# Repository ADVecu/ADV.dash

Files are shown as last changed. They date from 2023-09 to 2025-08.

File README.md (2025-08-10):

# ADV.dash

ADV.dash is a dashboard project built with **LVGL** and **ESP32-S3**.  
It is prepared to receive CAN bus data from **rusEFI** and, in the future, other programmable ECUs.

## Requirements
- PlatformIO
- ESP32-S3 DevKitC-1 board (1.5-inch display)
- LVGL library
- rusEFI CAN bus setup

## Compilation Steps
1. Clone the repository:
   ```bash
   git clone https://github.com/ADVecu/ADV.dash.git
   ```
2. Open the project in **PlatformIO**.
3. Copy the file `esp32-s3-devkitc-1-5inch` to the **boards** directory of the **Espressif** platform in PlatformIO.
4. Copy `lv_conf.h` to its correct LVGL configuration folder.
5. Build and upload the project to your ESP32-S3.

## Images
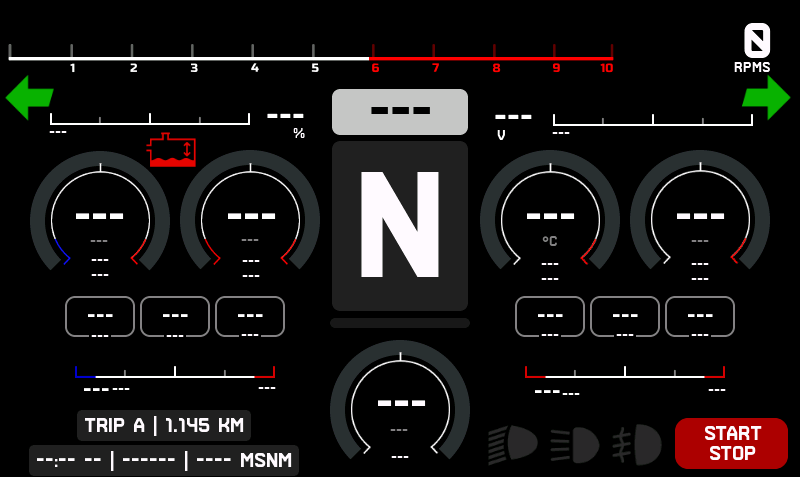
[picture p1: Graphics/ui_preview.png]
ADV.dash UI

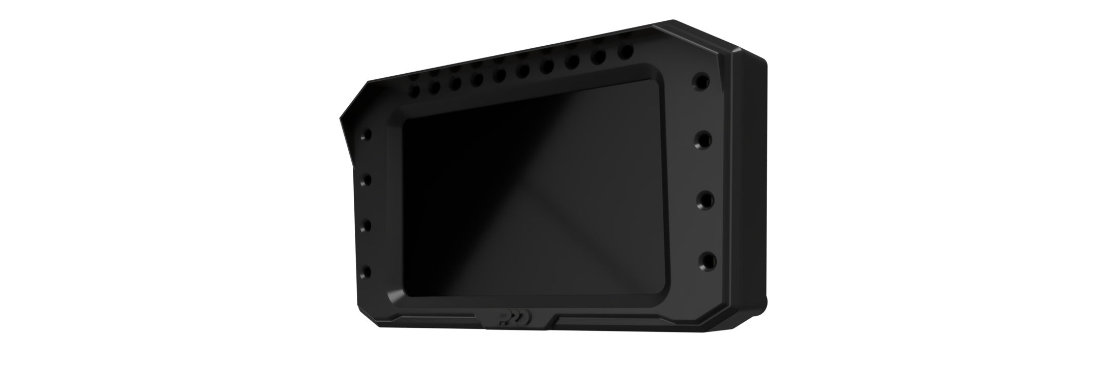
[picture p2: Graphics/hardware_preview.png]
ADV.dash Board


---

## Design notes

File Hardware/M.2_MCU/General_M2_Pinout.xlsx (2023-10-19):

 | MicroModule (M.2) Pinout v1.0 An Input is into the module. The module controls Outputs.
 |  | GND | 75 | Notes:
74 | 3.3V | G5 / BUS5 | 73 | All pins are 3.3V compatible unless otherwise specified. Don't expose any 3.3V pins to 5V.
72 | RTC_3V_BATT | G6 / BUS6 | 71 | Each MicroMod Processor Board has a GPIO controlled LED on the module not exposed to the board edge (aka LED_BUILTIN).
70 | G22 | G7 / BUS7 | 69 | A0/A1 should be assigned to pins that are exclusively ADC (no PWM capability)
68 | G21 | G8 | 67 | PWM0/PWM1 should be assigned to pins that are exclusively PWM (no ADC capability) D0/D1 should be assigned to pins that are exclusively GPIO (no ADC or PWM capability)
66 | G20 | G9 / ADC_D- / CAM_HSYNC | 65
64 | G19 | G10 / ADC_D+ / CAM_VSYNC | 63 | If the microcontroller lacks a specific pin function, and has left over GPIO, they can be over-ruled with
62 | G18 | SPI_CIPO (I) | 61 | GPIO. For example CTS/RTS can be overwritten with a GPIO if the microcontroller does not have flow control.
60 | G17 | SPI_COPI (O) | 59
58 | G16 | SPI_SCK (O) | 57
56 | G15 | SPI_CS# | 55
54 | G14 | I2C_SCL1 (I/O) | 53
52 | G13 | I2C_SDA1 (I/O) | 51
50 | G12 | BATT_VIN/3 (I - ADC) (0/3.3V) | 49
48 | G4 / BUS4 | PWM1 | 47
46 | G3 / BUS3 | GND | 45
44 | G2 / BUS2 | CAN_TX | 43
42 | G1 / BUS1 | CAN_RX | 41
40 | G0 / BUS0 | GND | 39
38 | A1 | USBHOST_D- | 37
36 | GND | USBHOST_D+ | 35
34 | A0 | GND | 33
32 | PWM0 | Module Key | 31
30 | Module Key | Module Key | 29
28 | Module Key | Module Key | 27
26 | Module Key | Module Key | 25
24 | Module Key | SWDIO | 23
22 | CAN2_TX | SWDCK | 21
20 | CAN2_RX | UART_RX1 (I) | 19
18 | D1 / CAM_TRIG | UART_TX1 (O) | 17
16 | I2C_INT# (I) | UART_CTS1 (I) | 15
14 | I2C_SCL (I/O) | UART_RTS1 (O) | 13
12 | I2C_SDA (I/O) | BOOT (I - Open Drain) | 11
10 | D0 | USB_VIN | 9
8 | G11 / SWDSWO | GND | 7
6 | RESET# (I - Open Drain) | USB_D- | 5
4 | 3.3V_EN | USB_D+ | 3
2 | 3.3V | GND | 1

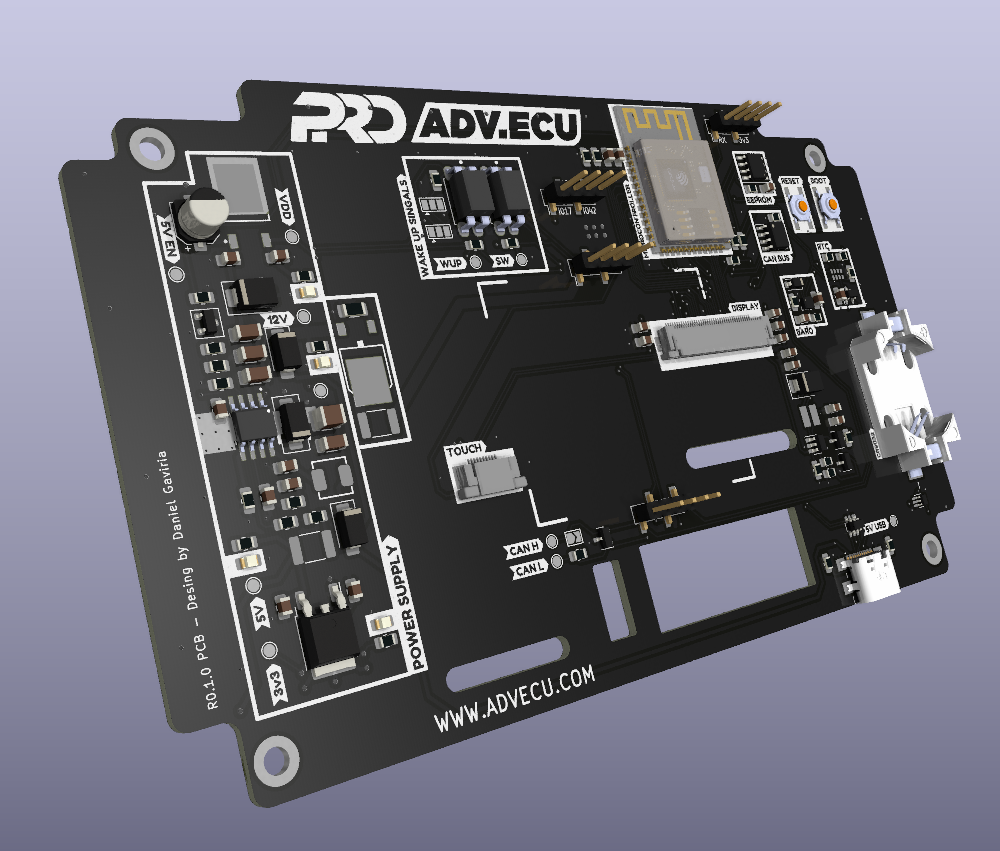
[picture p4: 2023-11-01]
Hardware/Dash/AdvDash_5_inch.png

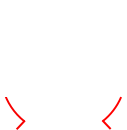
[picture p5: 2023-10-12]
SquerLine Project/assets/arcScaleRR.png

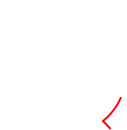
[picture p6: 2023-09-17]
SquerLine Project/assets/arcScale.png

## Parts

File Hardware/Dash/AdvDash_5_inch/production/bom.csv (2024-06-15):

Designator | Footprint | Quantity | Value | LCSC Part #
BT1 | BAT_CR2032-BS-6-1 | 1 | CR2032-BS-6-1 | C70377
C1, C12, C21, C23, C27, C7 | 0805 | 6 | 0.1uF | C38141
C10 | 1210 | 1 | 33uF | C531418
C11 | 1206 | 1 | 33uF | C342606
C13 | CP_Elec_5x5.4 | 1 | 100nF | C2992591
C14 | 0805 | 1 | 1uF - X7R | C116352
C15, C17 | 0805 | 2 | 22uF | C602037
C16, C20 | 0805 | 2 | 1uF | C28323
C18, C19 | 0805 | 2 | 100nF | C38141
C2, C22, C24, C25 | 0805 | 4 | 10uF | C15850
C26, C6 | 0805 | 2 | 10nF | C83170
C28, C29 | 0805 | 2 | 10uF | C1713
C3, C4 | 1206 | 2 | 4.7uF | C1872
C30, C31, C32, C33, C34, C35, C36, C37, C38, C39, C40, C41, C42, C43, C44, C45, C46, C47 | 0603 | 18 | 0.1uF | C577419
C5 | 1206 | 1 | 10nF | C106239
C8 | 0805 | 1 | 4.7nF | C1744
C9 | 0805 | 1 | 39pF | C1817
D1, D11 | D_SMA | 2 | 1N5819 | C437199
D10 | SOT-23 | 1 | BAS70-05 | C5189799
D12 | 0805 | 1 | LED | C965819
D13, D14, D15, D16, D17, D18, D19, D20, D21, D22, D23, D24, D25, D26, D27, D28, D29, D30 | LED_RGB_5050-6 | 18 | SK9822 | C2829089
D2 | D_SMA | 1 | B340 | C64982
D3, D4 | 0805 | 2 | LED | C965818
D5 | D_SMB | 1 | SMBJ20A | C151257
D6 | 0805 | 1 | LED | C965812
D7 | D_SMB | 1 | SS24BF | C35501
D8 | SOT-23 | 1 | NUP2105L | C5158054
D9 | D_SOD-123 | 1 | 1N4148W | C5345962
F1, F2 | 1812 | 2 | 3A 24V | C883154
G1 | INF-PG-TO252-3-11_N | 1 | TLF80511TF_V33
H1, H2, H3, H4 | MountingHole_3.2mm_M3_DIN965_Pad_TopBottom | 4 | MountingHole
H5, H6, H7 | MountingHole_2.5mm_Pad | 3 | MountingHole_Pad | C3020128
IC1 | RV8803C7 | 1 | RV-8803-C7 | C2846926
IC2, IC3 | SOT-353_SC-70-5_Handsoldering | 2 | 74HCT1G126GW,125 | C455064
J1 | 117348390 | 1 | 1-1734839-0 | C590935
J2 | 54104-4031 | 1 | 54104-4031 | C164172
J3 | USB4110GFA | 1 | USB4110-GF-A
J4, J6 | PinHeader_1x04_P2.54mm_Vertical_SMD_Pin1Left | 2 | 2.54mm 1x4
J5 | PinHeader_1x04_P2.54mm_Vertical_SMD_Pin1Left | 1 | UART0
JP1 | SolderJumper-2_P1.3mm_Open_TrianglePad1.0x1.5mm | 1 | 120ohm
JP2, JP3, JP4, JP6 | SolderJumper-3_P1.3mm_Open_Pad1.0x1.5mm | 4 | ACT +/-
JP5 | SolderJumper-3_P1.3mm_Open_Pad1.0x1.5mm | 1 | Reset Control
L1 | MDA4020-6R8M | 1 | 6.8uH | C2847472
L2 | TCK145 | 1 | 6.8uH | C167253
Q2 | SOT-23 | 1 | AO3401A | C15127
Q3 | SOT-23 | 1 | S8050 | C266592
R1, R12, R17, R2, R24, R26, R27, R35, R36, R7 | 0805 | 10 | 10K | C17414
R10 | 0805 | 1 | 0R | C17414
R13, R14 | 0805 | 2 | 1k3 | C2933303
R15 | 0805 | 1 | 10R | C25278
R16, R28, R29, R30, R31 | 0805 | 5 | 100k | C149504
R18 | 0805 | 1 | 100R | C17408
R19, R20 | 0805 | 2 | 4.7k | C17673
R21, R6 | 0805 | 2 | 0R | C17477
R22, R23 | 0805 | 2 | 5k1 | C84375
R25 | 0805 | 1 | 120 | C114245
R3 | 0805 | 1 | 332k | C212383
R32 | 0805 | 1 | 2k | C17604
R33, R34 | 0805 | 2 | 2K7 | C17530
R4 | 0805 | 1 | 68k1 | C5266070
R5 | 0805 | 1 | 49k9 | C17719
R8 | 0805 | 1 | 1k91 | C2999452
R9 | 1206 | 1 | 2K7 | C2907449
SW1, SW2 | SW_TL3342F160QG_TR | 2 | RESET | C2886898
T1 | D-PAK_TO252AA | 1 | IRFR5305 | C5155388
TP1 | TestPoint_Pad_D1.5mm | 1 | VIN_TP
TP10 | TestPoint_Pad_D1.5mm | 1 | CANH_TP
TP11 | TestPoint_Pad_D1.5mm | 1 | CANL_TP
TP2 | TestPoint_Pad_D1.5mm | 1 | EN_TP
TP3 | TestPoint_Pad_D1.5mm | 1 | EN_MCU_TP
TP4 | TestPoint_Pad_D1.5mm | 1 | USB_5VTP
TP5 | TestPoint_Pad_D1.5mm | 1 | 5V_TP
TP6 | TestPoint_Pad_D1.5mm | 1 | VDD_TP
TP7 | TestPoint_Pad_D1.5mm | 1 | 3.3V_TP
TP8 | TestPoint_Pad_D1.5mm | 1 | WAKE_UP_TP
TP9 | TestPoint_Pad_D1.5mm | 1 | SW12V_TP
U1 | ESP32-S3-WROOM-1 | 1 | ESP32-S3-WROOM-1-N4R8 | C2913200
U10, U9 | SOIC254P975X460-4N | 2 | PC817 | C3025164
U2 | CONV_TPS54331DDA | 1 | TPS54331DDA | C90761
U3 | SOT-23-6_Handsoldering | 1 | MT9201 | C182966
U4 | SOT-23-6 | 1 | USBLC6-2P6 | C7519
U5 | SOIC-8_3.9x4.9mm_P1.27mm | 1 | SN65HVD230 | C12084
U6 | Bosch_LGA-8_2x2.5mm_P0.65mm_ClockwisePinNumbering | 1 | BMP280 | C83291
U7 | SOIC-8-1EP_3.9x4.9mm_P1.27mm_EP2.29x3mm | 1 | CAT24C51 | C79986
U8 | TO-252-2 | 1 | LD1086DT33TR | C12051

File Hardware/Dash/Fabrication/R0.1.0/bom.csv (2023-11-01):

Designator | Footprint | Quantity | Value | LCSC Part #
BT1 | BAT_CR2032-BS-6-1 | 1 | CR2032-BS-6-1
C1, C12, C23, C27, C7 | 0805 | 5 | 0.1uF
C10 | 1210 | 1 | 33uF
C11 | 1206 | 1 | 33uF
C13 | CP_Elec_5x5.4 | 1 | 100nF
C14 | 0805 | 1 | 1uF - X7R
C15, C17 | 0805 | 2 | 22uF
C16, C20 | 0805 | 2 | 1uF
C18, C19 | 0805 | 2 | 100nF
C2, C22, C24, C25, C28, C29 | 0805 | 6 | 10uF
C21 | 0805 | 1 | 0.1uF | DNP
C26, C6 | 0805 | 2 | 10nF
C3, C4 | 1206 | 2 | 4.7uF
C30, C31, C32, C33, C34, C35, C36, C37, C38, C39, C40, C41, C42, C43, C44, C45, C46, C47 | 0603 | 18 | 0.1uF
C5 | 1206 | 1 | 10nF
C8 | 0805 | 1 | 4.7nF
C9 | 0805 | 1 | 39pF
D1, D11 | D_SMA | 2 | 1N5819
D10 | SOT-23 | 1 | BAS70-05
D12, D3, D4 | 0805 | 3 | LED
D13, D14, D15, D16, D17, D18, D19, D20, D21, D22, D23, D24, D25, D26, D27, D28, D29, D30 | LED_WS2812B_PLCC4_5.0x5.0mm_P3.2mm | 18 | WS2812B
D2 | D_SMA | 1 | B340
D5 | D_SMB | 1 | SMBJ20A
D6 | 0805 | 1 | LED | DNP
D7 | D_SMB | 1 | SS24BF
D8 | SOT-23 | 1 | NUP2105L
D9 | D_SOD-123 | 1 | 1N4148W
F1 | 1812 | 1 | 3A 24V
F2 | 1812 | 1 | 3A 24V | C883140
G1 | INF-PG-TO252-3-11_N | 1 | TLF80511TF_V33
H1, H2, H3, H4 | MountingHole_3.2mm_M3_DIN965_Pad_TopBottom | 4 | MountingHole
IC1 | RV8803C7 | 1 | RV-8803-C7
IC2 | SOT-353_SC-70-5_Handsoldering | 1 | 74HCT1G126GW,125
J1 | 117348390 | 1 | 1-1734839-0
J2 | 54104-4031 | 1 | 54104-4031
J3 | USB4110GFA | 1 | USB4110-GF-A
J4, J6 | PinHeader_1x04_P2.54mm_Vertical_SMD_Pin1Left | 2 | 2.54mm 1x4
J5 | PinHeader_1x04_P2.54mm_Vertical_SMD_Pin1Left | 1 | UART0
J7 | PinHeader_1x04_P2.54mm_Vertical_SMD_Pin1Left | 1 | AUX
JP1 | SolderJumper-2_P1.3mm_Open_TrianglePad1.0x1.5mm | 1 | 120ohm
JP2, JP3 | SolderJumper-3_P1.3mm_Open_Pad1.0x1.5mm | 2 | ACT +/-
L1 | MDA4020-6R8M | 1 | 6.8uH
L2 | TCK145 | 1 | 6.8uH
Q1 | SOT-23 | 1 | BSS139H6327XTSA1
Q2 | SOT-23 | 1 | AO3401A
Q3 | SOT-23 | 1 | S8050
R1, R10, R11, R12, R17, R2, R24, R26, R27, R7 | 0805 | 10 | 10K
R13, R14 | 0805 | 2 | 1k3
R15 | 0805 | 1 | 10R
R16, R28, R29, R30, R31 | 0805 | 5 | 100k
R18 | 0805 | 1 | 100R
R19, R20 | 0805 | 2 | 4.7k
R21 | 0805 | 1 | 0R
R22, R23 | 0805 | 2 | 5k1
R25 | 0805 | 1 | 120
R3 | 0805 | 1 | 332
R32 | 0805 | 1 | 2k
R33, R34 | 0805 | 2 | 2K7
R35, R36 | 0805 | 2 | 10K | DNP
R4 | 0805 | 1 | 68k1
R5 | 0805 | 1 | 49k9
R6 | 0805 | 1 | 0
R8 | 0805 | 1 | 1k91
R9 | 1206 | 1 | 2K7
SW1, SW2 | SW_TL3342F160QG_TR | 2 | RESET
T1 | D-PAK_TO252AA | 1 | IRFR5305 | C5155388
TP1 | TestPoint_Pad_D1.5mm | 1 | VIN_TP
TP10 | TestPoint_Pad_D1.5mm | 1 | CANH_TP
TP11 | TestPoint_Pad_D1.5mm | 1 | CANL_TP
TP2 | TestPoint_Pad_D1.5mm | 1 | EN_TP
TP3 | TestPoint_Pad_D1.5mm | 1 | EN_MCU_TP
TP4 | TestPoint_Pad_D1.5mm | 1 | USB_5VTP
TP5 | TestPoint_Pad_D1.5mm | 1 | 5V_TP
TP6 | TestPoint_Pad_D1.5mm | 1 | VDD_TP
TP7 | TestPoint_Pad_D1.5mm | 1 | 3.3V_TP
TP8 | TestPoint_Pad_D1.5mm | 1 | WAKE_UP_TP
TP9 | TestPoint_Pad_D1.5mm | 1 | SW12V_TP
U1 | ESP32-S3-WROOM-1 | 1 | ESP32-S3-WROOM-1
U10, U9 | SOIC254P975X460-4N | 2 | PC817
U2 | CONV_TPS54331DDA | 1 | TPS54331DDA
U3 | SOT-23-6_Handsoldering | 1 | MT9201
U4 | SOT-23-6 | 1 | USBLC6-2P6
U5 | SOIC-8_3.9x4.9mm_P1.27mm | 1 | SN65HVD230
U6 | Bosch_LGA-8_2x2.5mm_P0.65mm_ClockwisePinNumbering | 1 | BMP280
U7 | SOIC-8-1EP_3.9x4.9mm_P1.27mm_EP2.29x3mm | 1 | CAT24C51
U8 | TO-252-2 | 1 | LD1086DT33TR

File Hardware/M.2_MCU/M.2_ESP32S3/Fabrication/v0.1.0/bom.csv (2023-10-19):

Designator | Footprint | Quantity | Value | LCSC Part #
C1 | 0805 | 1 | 100nF
C2 | 0805 | 1 | 10uF
FRAME1 | CREATIVE_COMMONS | 1 | FRAME-LEDGER
J1 | M.2-CARD-E-22 | 1 | MICROMOD-2222
LOGO1 | ORDERING_INSTRUCTIONS | 1 | SPECIAL_INSTRUCTIONS-ORDERING
R1, R2 | 0805 | 2 | 10K
U1 | ESP32-S3-WROOM-1 | 1 | ESP32-S3-WROOM-1
kibuzzard-652F57BF | kibuzzard-652F57BF | 1 | G***

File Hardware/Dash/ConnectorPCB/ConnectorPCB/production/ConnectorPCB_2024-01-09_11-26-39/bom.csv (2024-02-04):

Designator | Footprint | Quantity | Value | LCSC Part #
_2, |  | 2
H5 | MountingHole_2.2mm_M2_Pad | 1 | MountingHole_Pad | C3020128
J1 | 7762761 | 1 | 776276-1
J2, J3 | PinHeader_1x04_P2.54mm_Vertical | 2 | 2.54mm 1x4

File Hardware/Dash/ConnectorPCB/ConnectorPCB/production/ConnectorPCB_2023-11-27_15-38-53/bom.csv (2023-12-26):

Designator | Footprint | Quantity | Value | LCSC Part #
J1 | 7762761 | 1 | 776276-1
J2, J3 | PinHeader_1x04_P2.54mm_Vertical | 2 | 2.54mm 1x4

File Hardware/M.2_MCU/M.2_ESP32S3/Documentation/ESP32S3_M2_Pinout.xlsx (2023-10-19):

 | MicroModule (M.2) Pinout v1.0 An Input is into the module. The module controls Outputs.
 |  | GND | 75 | Notes:
74 | 3.3V | G5 / BUS5 / GPIO5 | 73 | All pins are 3.3V compatible unless otherwise specified. Don't expose any 3.3V pins to 5V.
72 | X | G6 / BUS6 / GPIO6 | 71 | Each MicroMod Processor Board has a GPIO controlled LED on the module not exposed to the board edge (aka LED_BUILTIN).
70 | X | G7 / BUS7 / GPIO7 | 69 | A0/A1 should be assigned to pins that are exclusively ADC (no PWM capability)
68 | G21 / GPIO21 | G8 / GPIO46 | 67 | PWM0/PWM1 should be assigned to pins that are exclusively PWM (no ADC capability) D0/D1 should be assigned to pins that are exclusively GPIO (no ADC or PWM capability)
66 | G20 / GPIO45 | G9 / ADC_D- / CAM_HSYNC / GPIO47 | 65
64 | G19 / GPIO03 | G10 / ADC_D+ / CAM_VSYNC / GPIO48 | 63 | If the microcontroller lacks a specific pin function, and has left over GPIO, they can be over-ruled with
62 | G18 / GPIO18 | SPI_CIPO / GPIO13 | 61 | GPIO. For example CTS/RTS can be overwritten with a GPIO if the microcontroller does not have flow control.
60 | G17 / GPIO17 | SPI_COPI / GPIO11 | 59
58 | G16 / GPIO39 | SPI_SCK (O) / GPIO12 | 57
56 | G15 / GPIO02 | SPI_CS# / GPIO10 | 55 | 0, 8, 9, 10, 11, 12, 13, 15, 16, 19, 20, 40, 42, 43, 44
54 | G14 / GPIO16 | X | 53 | 27-38
52 | G13 / GPIO15 | X | 51
50 | G12 / GPIO14 | X | 49
48 | G4 / BUS4 / GPI14 | X | 47
46 | G3 / BUS3 / GPI41 | GND | 45
44 | G2 / BUS2 / GPI01 | CAN_TX / GPIO42 | 43
42 | G1 / BUS1 / GPI38 | CAN_RX / GPIO40 | 41
40 | X | GND | 39
38 | X | X | 37
36 | GND | X | 35
34 | X | GND | 33
32 | X | Module Key | 31
30 | Module Key | Module Key | 29
28 | Module Key | Module Key | 27
26 | Module Key | Module Key | 25
24 | Module Key | X | 23
22 | X | X | 21
20 | X | UART_RX1 / GPIO44 | 19
18 | X | UART_TX1 / GPIO43 | 17
16 | X | X | 15
14 | I2C_SCL (I/O) / GPIO9 | X | 13
12 | I2C_SDA (I/O) / GPIO8 | BOOT / GPIO0 | 11
10 | X | X | 9
8 | X | GND | 7
6 | RESET# / EN | USB_D- / GPIO19 | 5
4 | X | USB_D+ / GPIO20 | 3
2 | 3.3V | GND | 1

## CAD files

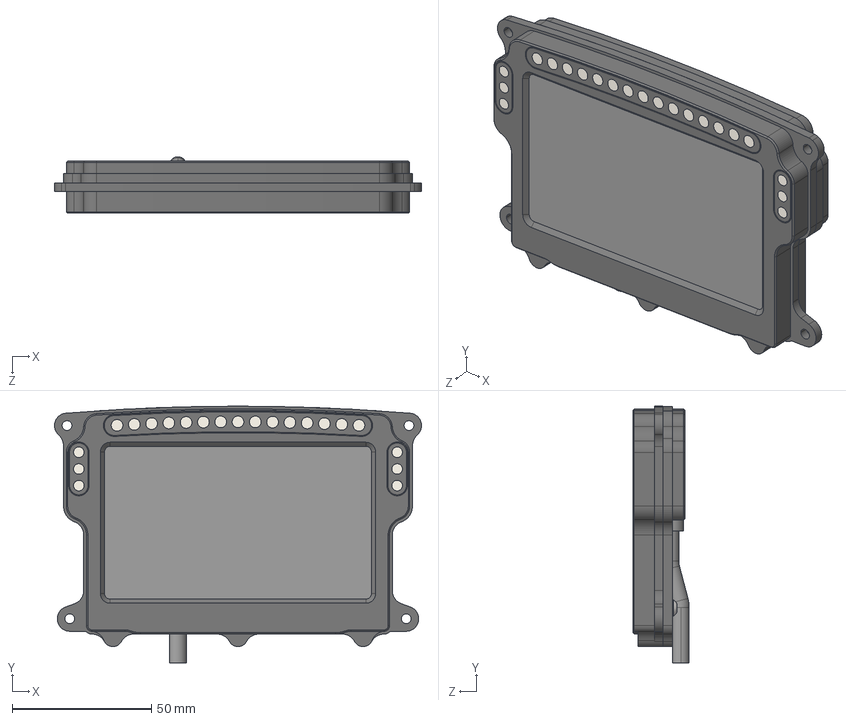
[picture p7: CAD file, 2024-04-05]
CAD Files/PCU-8D.STEP
132.0 x 92.4 x 20.3 mm
McLaren PCU-8D
M3 x 20_ISO 10642 - M5 x 25 - 25N x 8
socket button head screw_iso_ISO 7380 - M3 x 6 - 6N

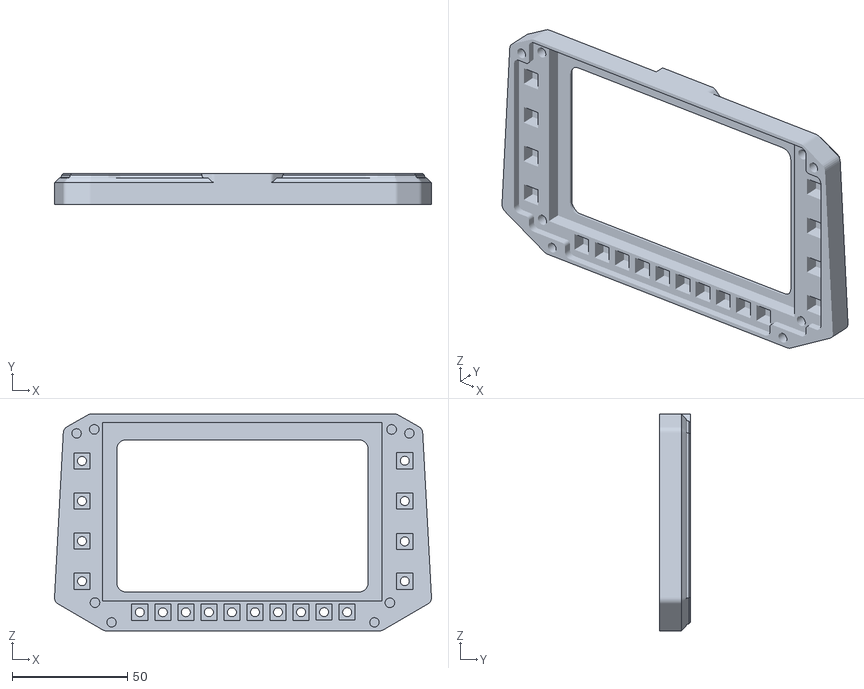
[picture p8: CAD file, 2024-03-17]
CAD Files/V2/DashSuperiorSinF.stl
163.5 x 13.6 x 94.1

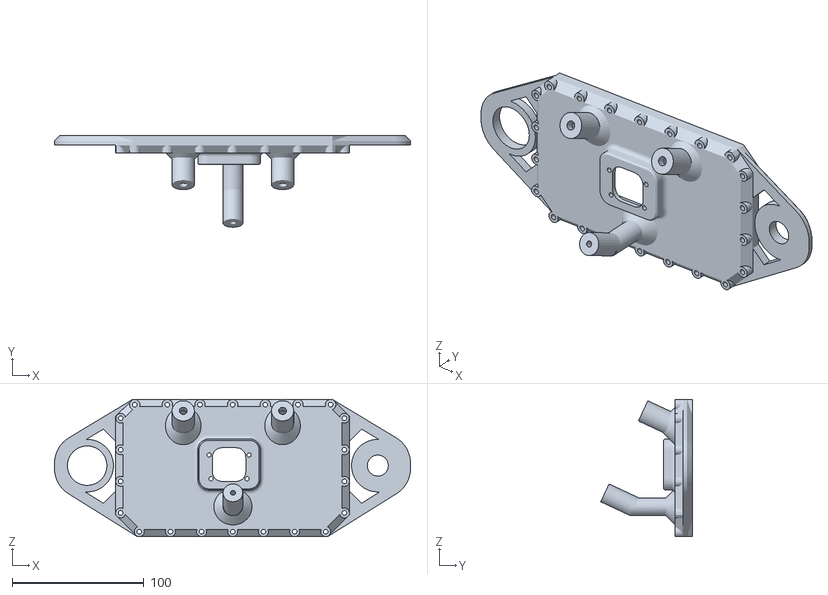
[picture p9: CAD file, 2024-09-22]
CAD Files/V3-AKT250/InferiorMotoOrejas.stl
270.6 x 69.6 x 104.3

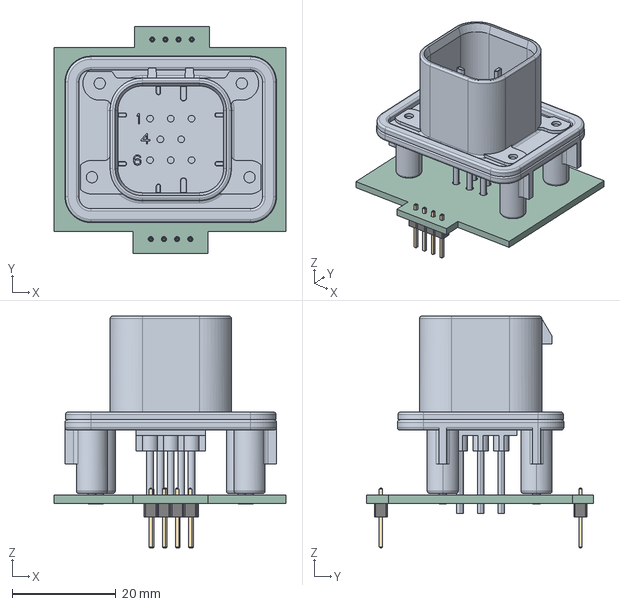
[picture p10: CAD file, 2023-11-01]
Hardware/Dash/ConnectorPCB/ConnectorPCB/ConnectorPCB.step
44.8 x 43.8 x 44.7 mm
ConnectorPCB PCB

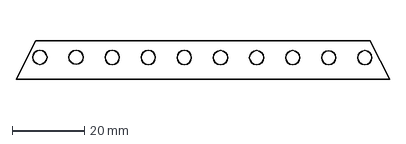
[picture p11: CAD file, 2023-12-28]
CAD Files/AcrilicoSUP2.dxf
103.3 x 10.7 mm

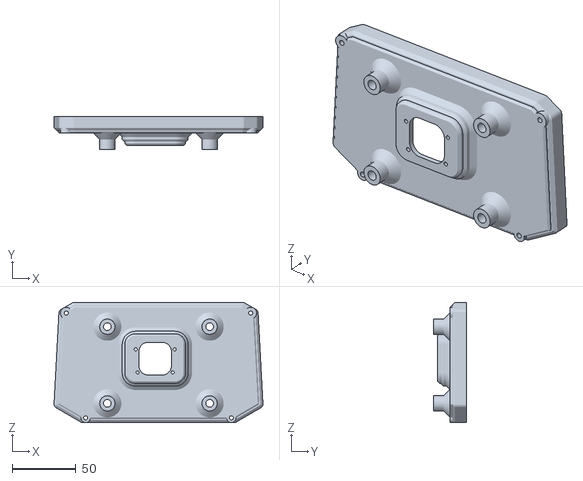
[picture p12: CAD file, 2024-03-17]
CAD Files/V2/DashInferior.stl
163.5 x 26.0 x 94.1

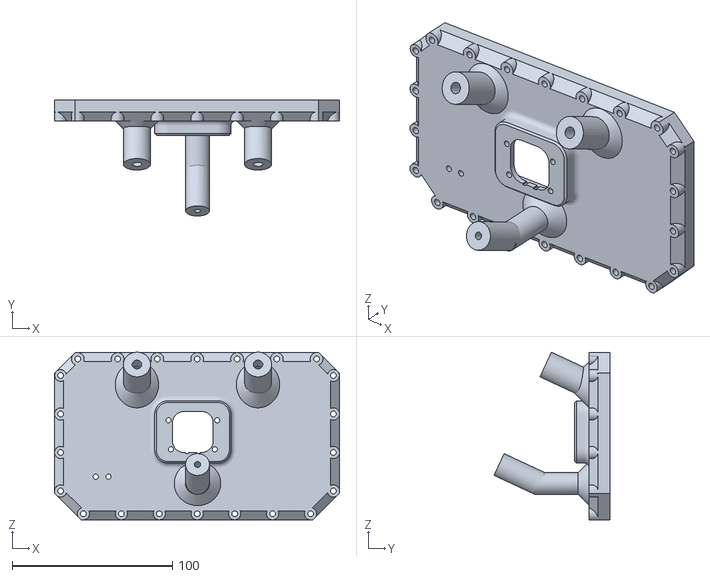
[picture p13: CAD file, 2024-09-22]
CAD Files/V3-AKT250/InferiorMoto.stl
177.7 x 72.4 x 104.6

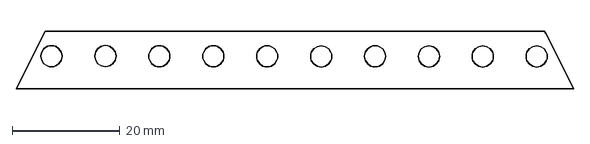
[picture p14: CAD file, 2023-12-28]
CAD Files/AcrilicoSUP.dxf
103.3 x 10.7 mm

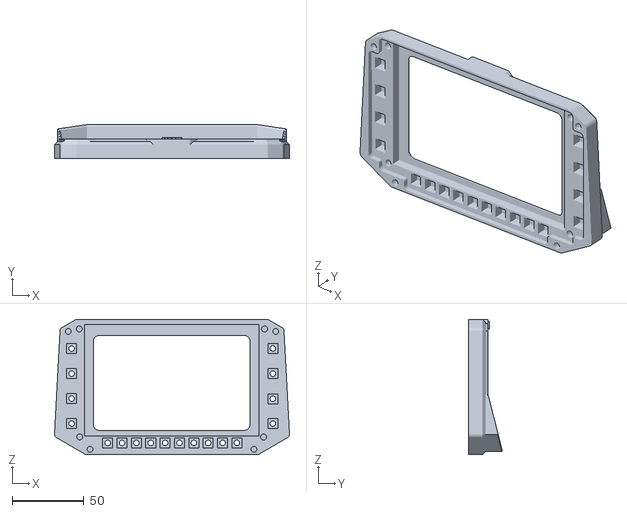
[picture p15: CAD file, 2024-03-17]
CAD Files/V2/DashSuperior.stl
163.5 x 23.5 x 94.1

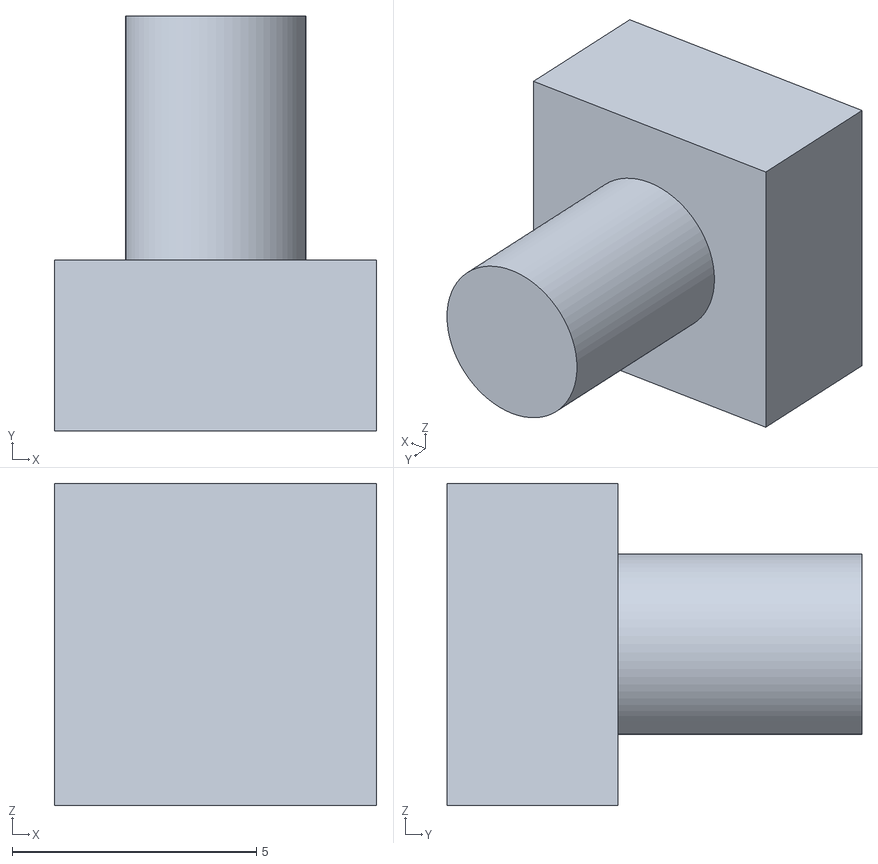
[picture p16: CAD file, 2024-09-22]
CAD Files/V3-AKT250/DifusorPequeno.stl
6.60 x 8.50 x 6.60

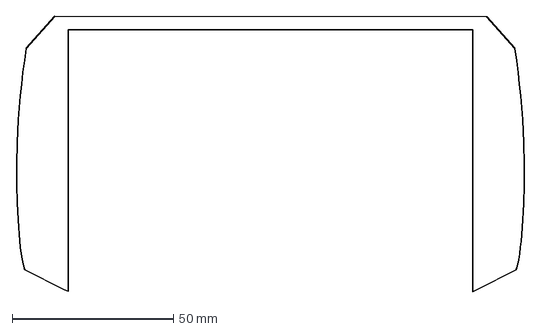
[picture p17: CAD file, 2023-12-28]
CAD Files/AcrilicoINF.dxf
157.5 x 85.2 mm

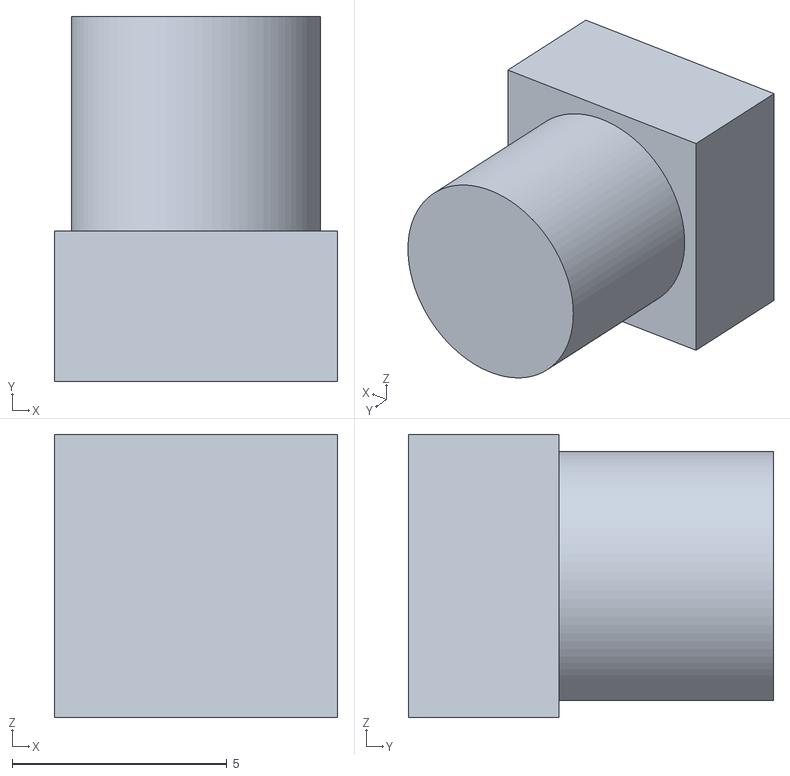
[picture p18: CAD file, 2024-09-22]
CAD Files/V3-AKT250/DifusorGrande.stl
6.60 x 8.50 x 6.60

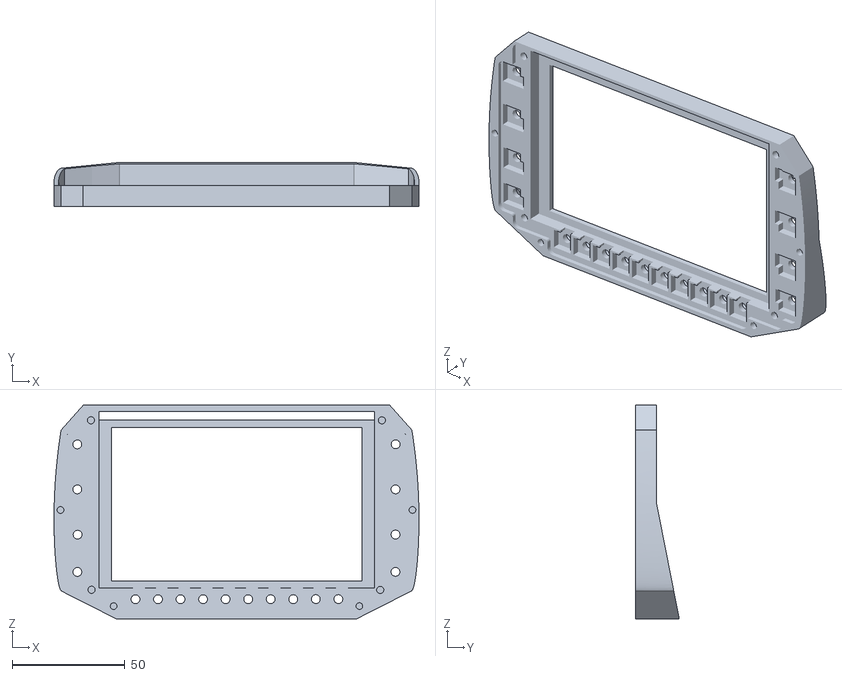
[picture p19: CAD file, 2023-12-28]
CAD Files/CaseSupV2.stl
161.7 x 19.3 x 94.7

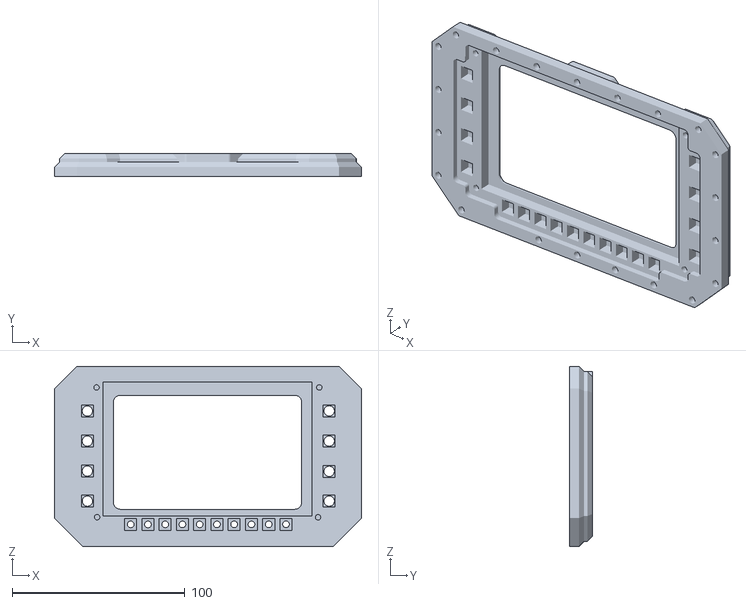
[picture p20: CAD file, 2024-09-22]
CAD Files/V3-AKT250/SuperiorV2.stl
177.7 x 13.6 x 104.3

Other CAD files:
CAD Files/Caseinf.stl
CAD Files/BenchTest.stl
CAD Files/CaseSup.stl
Hardware/Dash/AdvDash_5_inch/AdvDash_5_inch-B_Silkscreen.dxf
Hardware/Dash/AdvDash_5_inch/AdvDash_5_inch-F_Silkscreen.dxf
Hardware/Dash/AdvDash_5_inch/plots/AdvDash_5_inch-B_Silkscreen.dxf
Hardware/Dash/AdvDash_5_inch/plots/AdvDash_5_inch-F_Silkscreen.dxf

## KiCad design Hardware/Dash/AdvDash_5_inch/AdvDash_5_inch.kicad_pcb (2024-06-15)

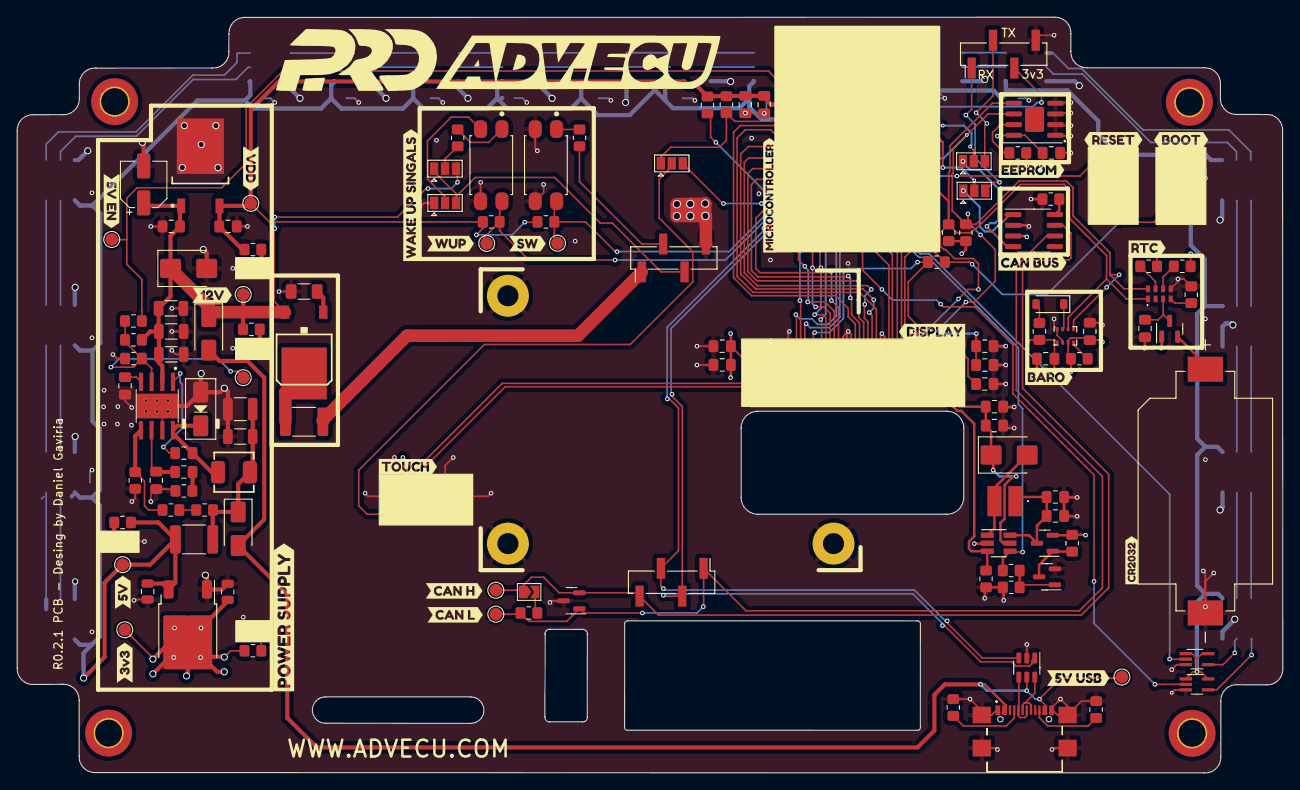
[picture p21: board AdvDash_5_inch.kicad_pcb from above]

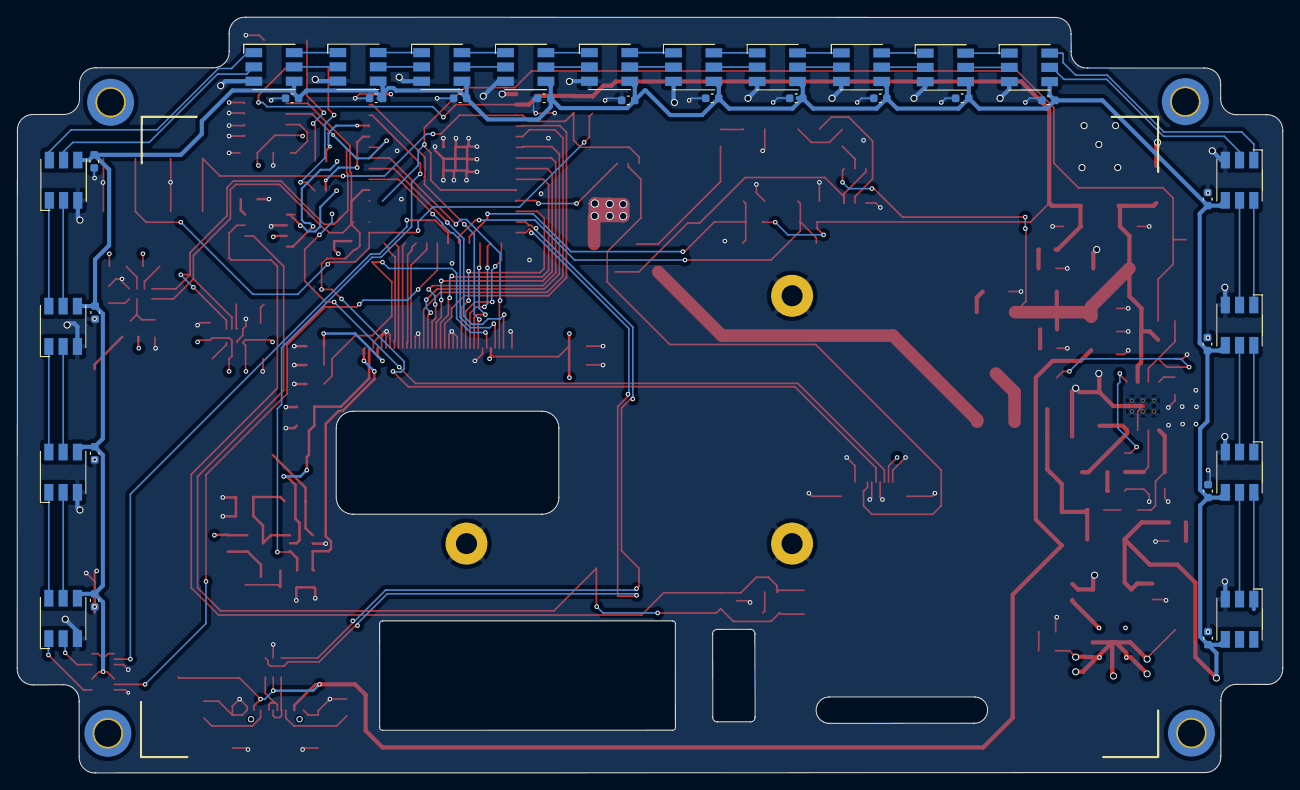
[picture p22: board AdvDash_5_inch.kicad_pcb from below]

Board: 4 copper layers, 150.6 x 89.9 mm, 188 parts (36 on the bottom side), 125 nets.

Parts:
BT1: CR2032-BS-6-1; BAT_CR2032-BS-6-1
C1, C7, C12, C21, C23, C27: 0.1uF; C_0805_2012Metric_Pad1.18x1.45mm_HandSolder
C2, C22, C24, C25: 10uF; C_0805_2012Metric_Pad1.18x1.45mm_HandSolder
C3, C4: 4.7uF; C_1206_3216Metric
C5: 10nF; C_1206_3216Metric
C6, C26: 10nF; C_0805_2012Metric_Pad1.18x1.45mm_HandSolder
C8: 4.7nF; C_0805_2012Metric_Pad1.18x1.45mm_HandSolder
C9: 39pF; C_0805_2012Metric_Pad1.18x1.45mm_HandSolder
C10: 33uF; C_1210_3225Metric
C11: 33uF; C_1206_3216Metric
C13: 100nF; CP_Elec_5x5.4
C14: 1uF - X7R; C_0805_2012Metric_Pad1.18x1.45mm_HandSolder
C15, C17: 22uF; C_0805_2012Metric_Pad1.18x1.45mm_HandSolder
C16, C20: 1uF; C_0805_2012Metric_Pad1.18x1.45mm_HandSolder
C18, C19: 100nF; C_0805_2012Metric_Pad1.18x1.45mm_HandSolder
C28, C29: 10uF; C_0805_2012Metric
C30, C31, C32, C33, C34, C35, C36, C37, C38, C39, C40, C41, C42, C43, C44, C45, C46, C47: 0.1uF; C_0603_1608Metric
D1, D11: 1N5819; D_SMA
D2: B340; D_SMA
D3, D4, D6, D12: LED; LED_0805_2012Metric_Pad1.15x1.40mm_HandSolder
D5: SMBJ20A; D_SMB
D7: SS24BF; D_SMB
D8: NUP2105L; SOT-23
D9: 1N4148W; D_SOD-123
D10: BAS70-05; SOT-23
D13, D14, D15, D16, D17, D18, D19, D20, D21, D22, D23, D24, D25, D26, D27, D28, D29, D30: SK9822; LED_RGB_5050-6
F1, F2: 3A 24V; Fuse_1812_4532Metric_Pad1.30x3.40mm_HandSolder
G1: TLF80511TF_V33; INF-PG-TO252-3-11_N
H1, H2, H3, H4: MountingHole; MountingHole_3.2mm_M3_DIN965_Pad_TopBottom
H5, H6, H7: MountingHole_Pad; MountingHole_2.5mm_Pad
IC1: RV-8803-C7; RV8803C7
IC2, IC3: 74HCT1G126GW,125; SOT-353_SC-70-5_Handsoldering
J1: 1-1734839-0; 117348390
J2: 54104-4031
J3: USB4110-GF-A; USB4110GFA
J4, J6: 2.54mm 1x4; PinHeader_1x04_P2.54mm_Vertical_SMD_Pin1Left
J5: UART0; PinHeader_1x04_P2.54mm_Vertical_SMD_Pin1Left
JP1: 120ohm; SolderJumper-2_P1.3mm_Open_TrianglePad1.0x1.5mm
JP2, JP3, JP4, JP6: ACT +/-; SolderJumper-3_P1.3mm_Open_Pad1.0x1.5mm
JP5: Reset Control; SolderJumper-3_P1.3mm_Open_Pad1.0x1.5mm
L1: 6.8uH; MDA4020-6R8M
L2: 6.8uH; TCK145
Q2: AO3401A; SOT-23
Q3: S8050; SOT-23
R1, R2, R7, R12, R17, R24, R26, R27, R35, R36: 10K; R_0805_2012Metric_Pad1.20x1.40mm_HandSolder
R3: 332k; R_0805_2012Metric_Pad1.20x1.40mm_HandSolder
R4: 68k1; R_0805_2012Metric_Pad1.20x1.40mm_HandSolder
R5: 49k9; R_0805_2012Metric_Pad1.20x1.40mm_HandSolder
R6, R10, R21: 0R; R_0805_2012Metric_Pad1.20x1.40mm_HandSolder
R8: 1k91; R_0805_2012Metric_Pad1.20x1.40mm_HandSolder
R9: 2K7; R_1206_3216Metric_Pad1.30x1.75mm_HandSolder
R13, R14: 1k3; R_0805_2012Metric_Pad1.20x1.40mm_HandSolder
R15: 10R; R_0805_2012Metric_Pad1.20x1.40mm_HandSolder
R16, R28, R29, R30, R31: 100k; R_0805_2012Metric_Pad1.20x1.40mm_HandSolder
R18: 100R; R_0805_2012Metric_Pad1.20x1.40mm_HandSolder
R19, R20: 4.7k; R_0805_2012Metric_Pad1.20x1.40mm_HandSolder
R22, R23: 5k1; R_0805_2012Metric_Pad1.20x1.40mm_HandSolder
R25: 120; R_0805_2012Metric_Pad1.20x1.40mm_HandSolder
R32: 2k; R_0805_2012Metric_Pad1.20x1.40mm_HandSolder
R33, R34: 2K7; R_0805_2012Metric_Pad1.20x1.40mm_HandSolder
SW1, SW2: RESET; SW_TL3342F160QG_TR
T1: IRFR5305; D-PAK_TO252AA
TP1: VIN_TP; TestPoint_Pad_D1.5mm
TP2: EN_TP; TestPoint_Pad_D1.5mm
TP3: EN_MCU_TP; TestPoint_Pad_D1.5mm
TP4: USB_5VTP; TestPoint_Pad_D1.5mm
TP5: 5V_TP; TestPoint_Pad_D1.5mm
TP6: VDD_TP; TestPoint_Pad_D1.5mm
TP7: 3.3V_TP; TestPoint_Pad_D1.5mm
TP8: WAKE_UP_TP; TestPoint_Pad_D1.5mm
TP9: SW12V_TP; TestPoint_Pad_D1.5mm
TP10: CANH_TP; TestPoint_Pad_D1.5mm
TP11: CANL_TP; TestPoint_Pad_D1.5mm
U1: ESP32-S3-WROOM-1-N4R8; ESP32-S3-WROOM-1
U2: TPS54331DDA; CONV_TPS54331DDA
U3: MT9201; SOT-23-6_Handsoldering
U4: USBLC6-2P6; SOT-23-6
U5: SN65HVD230; SOIC-8_3.9x4.9mm_P1.27mm
U6: BMP280; Bosch_LGA-8_2x2.5mm_P0.65mm_ClockwisePinNumbering
U7: CAT24C51; SOIC-8-1EP_3.9x4.9mm_P1.27mm_EP2.29x3mm
U8: LD1086DT33TR; TO-252-2
U9, U10: PC817; SOIC254P975X460-4N
kibuzzard-653B3D6F: G***; kibuzzard-653B3D6F
kibuzzard-653B3D82: G***; kibuzzard-653B3D82
kibuzzard-653B3DF4: G***; kibuzzard-653B3DF4
kibuzzard-653B3E73: G***; kibuzzard-653B3E73
kibuzzard-653B3E80: G***; kibuzzard-653B3E80
kibuzzard-653B3ED4: G***; kibuzzard-653B3ED4
kibuzzard-653B3EE1: G***; kibuzzard-653B3EE1
kibuzzard-653B3EFA: G***; kibuzzard-653B3EFA
kibuzzard-653B3F30: G***; kibuzzard-653B3F30
kibuzzard-653B3F43: G***; kibuzzard-653B3F43
kibuzzard-653B3FA3: G***; kibuzzard-653B3FA3
kibuzzard-653B3FD4: G***; kibuzzard-653B3FD4
kibuzzard-653B40B3: G***; kibuzzard-653B40B3
kibuzzard-653B41DD: G***; kibuzzard-653B41DD
kibuzzard-653B42DB: G***; kibuzzard-653B42DB
kibuzzard-653B414E: G***; kibuzzard-653B414E
kibuzzard-653B423C: G***; kibuzzard-653B423C
kibuzzard-653B435E: G***; kibuzzard-653B435E
kibuzzard-653B445A: G***; kibuzzard-653B445A
kibuzzard-653B4004: G***; kibuzzard-653B4004
kibuzzard-653B4099: G***; kibuzzard-653B4099
kibuzzard-653B4196: G***; kibuzzard-653B4196

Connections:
+3.3V: C19.1, C20.1, C22.1, C23.1, C24.1, C25.1, C27.2, C29.1, D10.1 (A2), J1.2, J2.10, J2.37, Q2.2 (S), R13.2, R16.1, R19.1, R20.2, R26.2, R27.2, R29.1, R30.1, TP7.1, U5.3 (VCC), U6.6 (VDDIO), U6.8 (VDD), U7.8 (VCC), U8.2 (OUT)
+5V: C28.1, C30.2, C31.2, C32.2, C33.2, C34.2, C35.2, C36.2, C37.2, C38.2, C39.2, C40.2, C41.2, C42.2, C43.2, C44.2, C45.2, C46.2, C47.2, D13.4 (VCC), D14.4 (VCC), D15.4 (VCC), D16.4 (VCC), D17.4 (VCC), D18.4 (VCC), D19.4 (VCC), D20.4 (VCC), D21.4 (VCC), D22.4 (VCC), D23.4 (VCC), D24.4 (VCC), D25.4 (VCC), D26.4 (VCC), D27.4 (VCC), D28.4 (VCC), D29.4 (VCC), D30.4 (VCC), F1.2, IC2.1 (OE), IC2.5 (VCC), IC3.1 (OE), IC3.5 (VCC), R32.2, TP5.1, U8.3 (IN)
/CAN_H: D8.2 (K), J4.4, JP1.1 (A), TP10.1, U5.7 (CANH)
/CAN_L: D8.1 (K), J4.1, R25.1, TP11.1, U5.6 (CANL)
/Can Bus/CRX: JP4.1 (A), U5.4 (R)
/Can Bus/CTX: JP6.1 (A), U5.1 (D)
/Connector/SW_12V: J6.2, R34.1
/Connector/WAKE_UP: J6.3, JP2.1 (A), JP3.3 (B)
/Display/B3: J2.17, U1.12 (GPIO8/TOUCH8/ADC1_CH7/SUBSPICS1)
/Display/B4: J2.16, U1.15 (GPIO3/TOUCH3/ADC1_CH2)
/Display/B5: J2.15, U1.16 (GPIO46)
/Display/B6: J2.14, U1.17 (GPIO9/TOUCH9/ADC1_CH8/FSPIHD/SUBSPIHD)
/Display/B7: J2.13, U1.39 (GPIO1/TOUCH1/ADC1_CH0)
/Display/DCLK: R2.1, R21.2, SW2.1, SW2.2, U1.27 (GPIO0/BOOT)
/Display/DE: J2.7, U1.33 (MTDO/GPIO40/CLK_OUT2)
/Display/G2: J2.26, U1.5 (GPIO5/TOUCH5/ADC1_CH4)
/Display/G3: J2.25, U1.6 (GPIO6/TOUCH6/ADC1_CH5)
/Display/G4: J2.24, U1.7 (GPIO7/TOUCH7/ADC1_CH6)
/Display/G5: J2.23, U1.8 (GPIO15/U0RTS/ADC2_CH4/XTAL_32K_P)
/Display/G6: J2.22, U1.9 (GPIO16/U0CTS/ADC2_CH5/XTAL_32K_N)
/Display/G7: J2.21, U1.4 (GPIO4/TOUCH4/ADC1_CH3)
/Display/HSYNC: J2.9, U1.32 (MTCK/GPIO39/CLK_OUT3/SUBSPICS1)
/Display/LCD_BL_CTR: R18.1, U1.38 (GPIO2/TOUCH2/ADC1_CH1), U3.4 (EN)
/Display/LCD_LEDA: C17.1, C18.1, D7.1 (K), J2.39, U3.5 (OV)
/Display/LCD_LEDK: J2.40, R15.2, U3.3 (FB)
/Display/R3: J2.33, U1.26 (GPIO45)
/Display/R4: J2.32, U1.25 (GPIO48/SPICLK_N/SUBSPICLK_N_DIFF)
/Display/R5: J2.31, U1.24 (GPIO47/SPICLK_P/SUBSPICLK_P_DIFF)
/Display/R6: J2.30, U1.23 (GPIO21)
/Display/R7: J2.29, U1.22 (GPIO14/TOUCH14/ADC2_CH3/FSPIWP/FSPIDQS/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)
/Display/TP_RST: JP5.1 (A), R1.1, SW1.1, SW1.2, U1.3 (EN)
/Display/TP_RST_2: JP5.3 (B), U1.11 (GPIO18/U1RXD/ADC2_CH7/CLK_OUT3)
/Display/VSYNC: J2.8, U1.34 (MTDI/GPIO41/CLK_OUT1)
/LEDs/WLED_CLK: IC2.2 (A), U1.20 (GPIO12/TOUCH12/ADC2_CH1/FSPICLK/FSPIIO6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)
/LEDs/WLED_CRT: IC3.2 (A), U1.21 (GPIO13/TOUCH13/ADC2_CH2/FSPIQ/FSPIIO7/S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)
/MCU/5V_EN: R10.1, TP3.1, U1.10 (GPIO17/U1TXD/ADC2_CH6)
/MCU/SW_12V: R36.1, TP9.1, U1.18 (GPIO10/TOUCH10/ADC1_CH9/FSPICS0/FSPIIO4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), U10.4
/MCU/U0RXD: J5.1, JP6.3 (B)
/MCU/U0TXD: J5.2, JP4.3 (B)
/MCU/WAKE_UP: R35.1, TP8.1, U1.19 (GPIO11/TOUCH11/ADC2_CH0/FSPID/FSPIIO5/S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), U9.4
/Power Supply/VIN/15_PROT: C3.1, C4.1, C5.1, C12.2, C13.1, D5.1 (K), D11.1 (K), G1.1 (I), JP2.3 (B), R3.1, R12.2, T1.3, TP1.1, U2.2 (VIN)
/SCL: IC1.8 (SCL), J1.3, R19.2, U1.35 (MTMS/GPIO42), U6.4 (SCK), U7.6 (SCL)
/SDA: IC1.1 (SDA), J1.5, R20.1, U1.31 (GPIO38/FSPIWP/SUBSPIWP), U6.3 (SDI), U7.5 (SDA)
/USB5V: D1.2 (A), D11.2 (A), J3.A4 (VBUS), J3.A9 (VBUS), J3.B4 (VBUS), J3.B9 (VBUS), TP4.1, U4.5 (VBUS)
/USBC/D+: J3.A6 (Dp1), J3.B6 (Dp2), J4.2, U1.14 (GPIO20/U1CTS/ADC2_CH9/CLK_OUT1/USB_D+), U4.1 (I/O1), U4.6 (I/O1)
/USBC/D-: J3.A7 (Dn1), J3.B7 (Dn2), J4.3, U1.13 (GPIO19/U1RTS/ADC2_CH8/CLK_OUT2/USB_D-), U4.3 (I/O2), U4.4 (I/O2)
/VIN15: F2.2, J6.1
GND: BT1.N, C1.2, C2.2, C3.2, C4.2, C5.2, C6.2, C9.2, C10.2, C11.2, C12.1, C13.2, C14.2, C15.2, C16.2, C17.2, C18.2, C19.2, C20.2, C21.2, C22.2, C23.2, C24.2, C25.2, C26.2, C27.1, C28.2, C29.2, C30.1, C31.1, C32.1, C33.1, C34.1, C35.1, C36.1, C37.1, C38.1, C39.1, C40.1, C41.1, C42.1, C43.1, C44.1, C45.1, C46.1, C47.1, D2.2 (A), D3.1 (K), D4.1 (K), D5.2 (A), D6.1 (K), D8.3 (A), D12.1 (K), D13.3 (GND), D14.3 (GND), D15.3 (GND), D16.3 (GND), D17.3 (GND), D18.3 (GND), D19.3 (GND), D20.3 (GND), D21.3 (GND), D22.3 (GND), D23.3 (GND), D24.3 (GND), D25.3 (GND), D26.3 (GND), D27.3 (GND), D28.3 (GND), D29.3 (GND), D30.3 (GND), G1.2 (GND), H5.1, H6.1, H7.1, IC1.5 (VSS), IC2.3 (GND), IC3.3 (GND), J1.1, J1.4, J1.6, J1.10, J1.MP1, J1.MP2, J2.5, J2.12, J2.18, J2.19, J2.20, J2.27, J2.28, J2.34, J2.35, J2.36, J2.38, J3.A1 (GND), J3.A12 (GND), J3.B1 (GND), J3.B12 (GND), J3.MP1, J3.MP2, J3.MP3, J3.MP4, J5.4, J6.4, JP3.1 (A), Q3.2 (E), R4.2, R5.2, R8.2, R9.2, R15.1, R17.2, R22.1, R23.2, R24.1, R28.2, R31.2, SW1.3, SW1.4, SW2.3, SW2.4, U1.1 (GND), U1.40 (GND), U1.41 (GND), U2.7 (GND), U2.9 (POWERPAD), U2.10 (GND), U2.11 (GND), U2.12 (GND), U2.13 (GND), U2.14 (GND), U2.15 (GND), U3.2 (GND), U4.2 (GND), U5.2 (GND), U6.1 (GND), U6.7 (GND), U7.1 (A0), U7.2 (A1), U7.3 (A2), U7.4 (GND), U8.1 (ADJ/GND), U9.3, U10.2, U10.3
unnamed: C8.2, R5.1
unnamed: C21.1, J2.11, R21.1
unnamed: C10.1, C11.1, D1.1 (K), F1.1, L1.2, R6.1
unnamed: C7.2, D2.1 (K), L1.1, U2.8 (PH)
unnamed: D3.2 (A), R12.1
unnamed: D4.2 (A), R13.1
unnamed: D6.2 (A), R14.1
unnamed: D7.2 (A), L2.2, U3.1 (SW)
unnamed: D9.2 (A), R26.1
unnamed: D9.1 (K), U6.2 (CSB)
unnamed: BT1.P, D10.2 (A1)
unnamed: C26.1, D10.3 (K), IC1.3 (VDD)
unnamed: D12.2 (A), R32.1
unnamed: D13.2 (CI), IC2.4 (Y)
unnamed: D13.5 (CO), D14.2 (CI)
unnamed: D13.1 (DI), IC3.4 (Y)
unnamed: D13.6 (DO), D14.1 (DI)
unnamed: D14.5 (CO), D15.2 (CI)
unnamed: D14.6 (DO), D15.1 (DI)
unnamed: D15.5 (CO), D16.2 (CI)
unnamed: D15.6 (DO), D16.1 (DI)
unnamed: D16.5 (CO), D17.2 (CI)
unnamed: D16.6 (DO), D17.1 (DI)
unnamed: D17.5 (CO), D18.2 (CI)
unnamed: D17.6 (DO), D18.1 (DI)
unnamed: D18.5 (CO), D19.2 (CI)
unnamed: D18.6 (DO), D19.1 (DI)
unnamed: D19.5 (CO), D20.2 (CI)
unnamed: D19.6 (DO), D20.1 (DI)
unnamed: D20.5 (CO), D21.2 (CI)
unnamed: D20.6 (DO), D21.1 (DI)
unnamed: D21.5 (CO), D22.2 (CI)
unnamed: D21.6 (DO), D22.1 (DI)
unnamed: D22.5 (CO), D23.2 (CI)
unnamed: D22.6 (DO), D23.1 (DI)
unnamed: D23.5 (CO), D24.2 (CI)
unnamed: D23.6 (DO), D24.1 (DI)
unnamed: D24.5 (CO), D25.2 (CI)
unnamed: D24.6 (DO), D25.1 (DI)
unnamed: D25.5 (CO), D26.2 (CI)
unnamed: D25.6 (DO), D26.1 (DI)
unnamed: D26.5 (CO), D27.2 (CI)
unnamed: D26.6 (DO), D27.1 (DI)
unnamed: D27.5 (CO), D28.2 (CI)
unnamed: D27.6 (DO), D28.1 (DI)
unnamed: D28.5 (CO), D29.2 (CI)
unnamed: D28.6 (DO), D29.1 (DI)
unnamed: D29.5 (CO), D30.2 (CI)
unnamed: D29.6 (DO), D30.1 (DI)
unnamed: F2.1, T1.4
unnamed: IC1.4 (CLKOE), R28.1
unnamed: IC1.7 (EVI), R29.2
unnamed: IC1.6 (~INT), R30.2
unnamed: J3.A5 (CC1), R22.2
unnamed: J3.B5 (CC2), R23.1
unnamed: JP1.2 (B), R25.2
unnamed: JP2.2 (C), R33.1
unnamed: JP3.2 (C), U9.2
unnamed: JP4.2 (C), U1.37 (U0TXD/GPIO43/CLK_OUT1)
unnamed: J1.7, JP5.2 (C)
unnamed: JP6.2 (C), U1.36 (U0RXD/GPIO44/CLK_OUT2)
unnamed: C15.1, C16.1, L2.1, Q2.3 (D), U3.6 (VIN)
unnamed: Q2.1 (G), Q3.3 (C), R16.2
unnamed: Q3.1 (B), R17.1, R18.2
unnamed: R6.2, R7.1
unnamed: R9.1, T1.1
unnamed: R33.2, U9.1
unnamed: R34.2, U10.1
unnamed: C7.1, U2.1 (BOOT)
unnamed: C8.1, C9.1, U2.6 (COMP)
unnamed: R3.2, R4.1, R10.2, TP2.1, U2.3 (EN)
unnamed: C6.1, U2.4 (SS)
unnamed: R7.2, R8.1, U2.5 (VSENSE)
unnamed: R24.2, U5.8 (Rs)
unnamed: R27.1, U6.5 (SDO)
unnamed: R31.1, U7.7 (WP)
VDD: C1.1, C2.1, C14.1, G1.3 (Q), J5.3, R1.2, R2.2, R14.2, R35.2, R36.2, TP6.1, U1.2 (3V3)

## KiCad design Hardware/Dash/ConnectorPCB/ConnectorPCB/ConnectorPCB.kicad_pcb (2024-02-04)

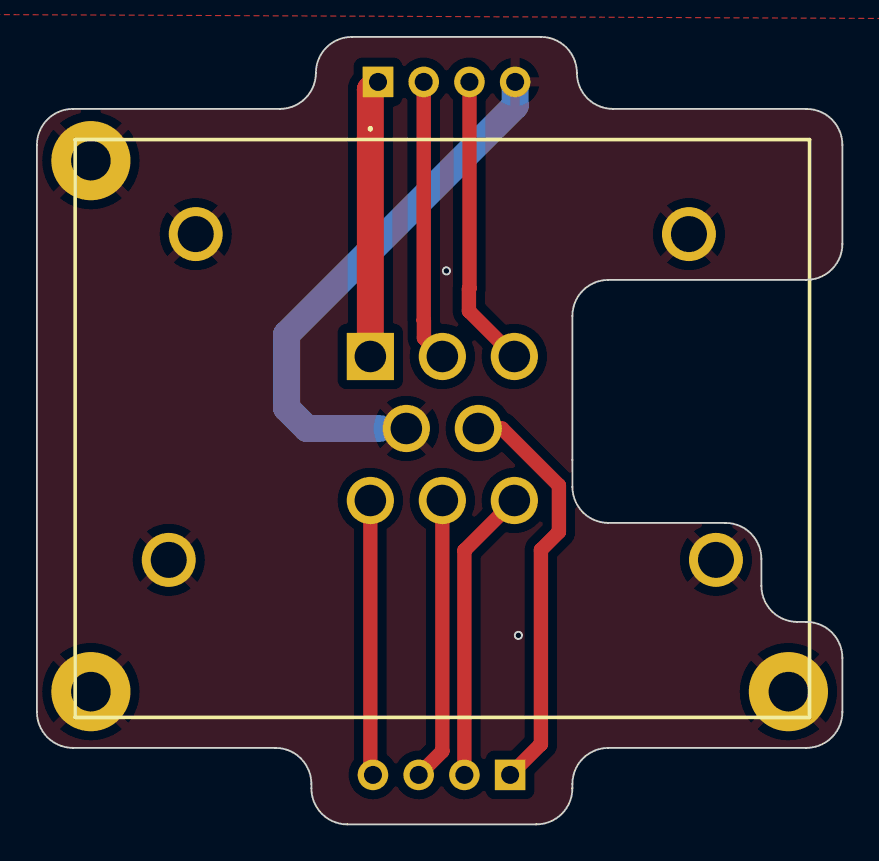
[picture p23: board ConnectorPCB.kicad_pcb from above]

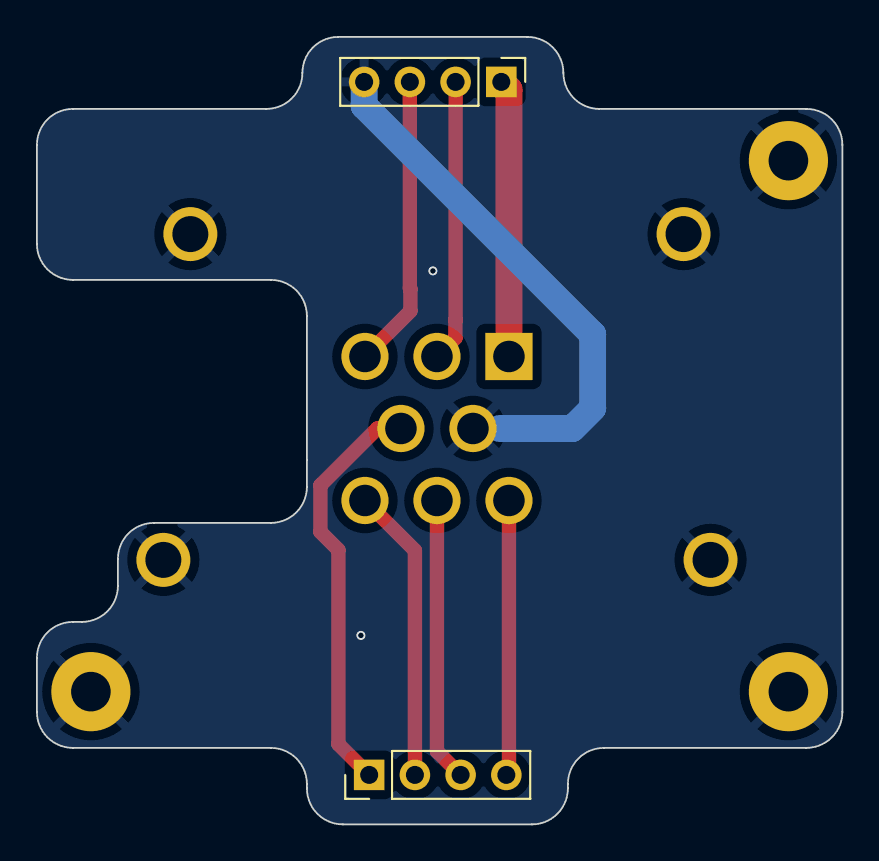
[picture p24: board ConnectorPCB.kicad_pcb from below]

Board: 2 copper layers, 44.8 x 43.8 mm, 4 parts (2 on the bottom side), 8 nets.

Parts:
H5: MountingHole_Pad; MountingHole_2.2mm_M2_Pad
J1: 776276-1; 7762761
J2, J3: 2.54mm 1x4; PinHeader_1x04_P2.54mm_Vertical

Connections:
CAN_H: J1.6, J3.4
CAN_L: J1.5, J3.1
D+: J1.7, J3.3
D-: J1.8, J3.2
GND: H5.1, J1.4, J1.MH1, J1.MH2, J1.MH3, J1.MH4, J2.4
SW_12V: J1.2, J2.2
VIN/15V: J1.1, J2.1
WAKE_UP: J1.3, J2.3

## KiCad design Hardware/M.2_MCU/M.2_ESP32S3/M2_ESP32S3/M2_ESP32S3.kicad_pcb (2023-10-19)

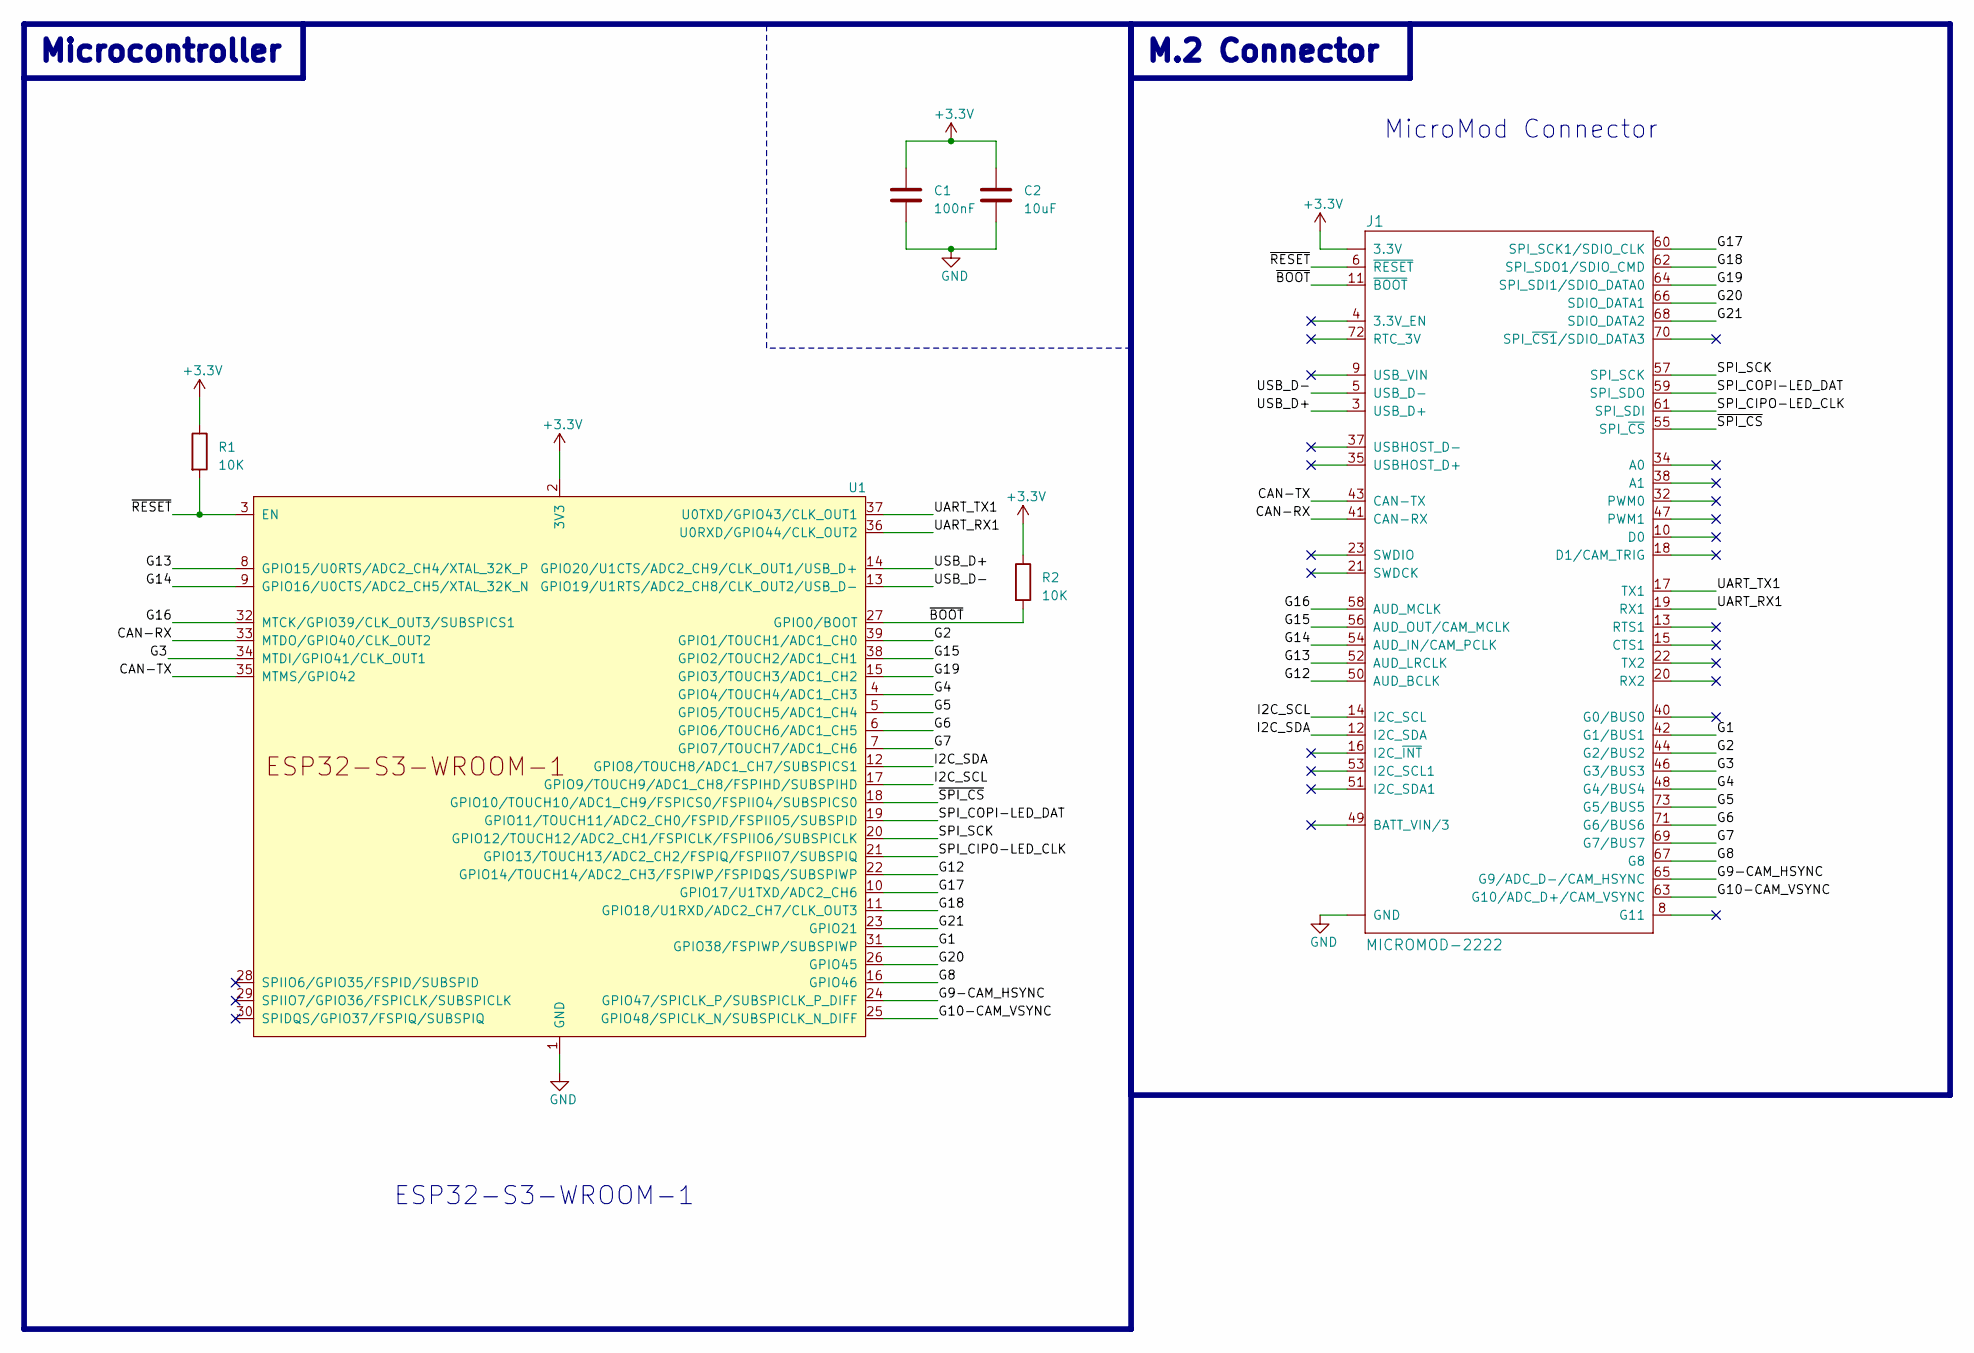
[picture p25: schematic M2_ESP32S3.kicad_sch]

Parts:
C1: 100nF; C_0805_2012Metric_Pad1.18x1.45mm_HandSolder
C2: 10uF; C_0805_2012Metric_Pad1.18x1.45mm_HandSolder
J1: MICROMOD-2222; M.2-CARD-E-22
R1, R2: 10K; R_0805_2012Metric_Pad1.15x1.40mm_HandSolder
U1: ESP32-S3-WROOM-1

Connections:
+3.3V: C1.1, C2.1, J1.2 (3.3V), J1.74 (3.3V), R1.1, R2.1, U1.2 (3V3)
/CAN-RX: J1.41 (CAN-RX), U1.33 (MTDO/GPIO40/CLK_OUT2)
/CAN-TX: J1.43 (CAN-TX), U1.35 (MTMS/GPIO42)
/G1: J1.42 (G1/BUS1), U1.31 (GPIO38/FSPIWP/SUBSPIWP)
/G2: J1.44 (G2/BUS2), U1.39 (GPIO1/TOUCH1/ADC1_CH0)
/G3: J1.46 (G3/BUS3), U1.34 (MTDI/GPIO41/CLK_OUT1)
/G4: J1.48 (G4/BUS4), U1.4 (GPIO4/TOUCH4/ADC1_CH3)
/G5: J1.73 (G5/BUS5), U1.5 (GPIO5/TOUCH5/ADC1_CH4)
/G6: J1.71 (G6/BUS6), U1.6 (GPIO6/TOUCH6/ADC1_CH5)
/G7: J1.69 (G7/BUS7), U1.7 (GPIO7/TOUCH7/ADC1_CH6)
/G8: J1.67 (G8), U1.16 (GPIO46)
/G9-CAM_HSYNC: J1.65 (G9/ADC_D-/CAM_HSYNC), U1.24 (GPIO47/SPICLK_P/SUBSPICLK_P_DIFF)
/G10-CAM_VSYNC: J1.63 (G10/ADC_D+/CAM_VSYNC), U1.25 (GPIO48/SPICLK_N/SUBSPICLK_N_DIFF)
/G12: J1.50 (AUD_BCLK), U1.22 (GPIO14/TOUCH14/ADC2_CH3/FSPIWP/FSPIDQS/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)
/G13: J1.52 (AUD_LRCLK), U1.8 (GPIO15/U0RTS/ADC2_CH4/XTAL_32K_P)
/G14: J1.54 (AUD_IN/CAM_PCLK), U1.9 (GPIO16/U0CTS/ADC2_CH5/XTAL_32K_N)
/G15: J1.56 (AUD_OUT/CAM_MCLK), U1.38 (GPIO2/TOUCH2/ADC1_CH1)
/G16: J1.58 (AUD_MCLK), U1.32 (MTCK/GPIO39/CLK_OUT3/SUBSPICS1)
/G17: J1.60 (SPI_SCK1/SDIO_CLK), U1.10 (GPIO17/U1TXD/ADC2_CH6)
/G18: J1.62 (SPI_SDO1/SDIO_CMD), U1.11 (GPIO18/U1RXD/ADC2_CH7/CLK_OUT3)
/G19: J1.64 (SPI_SDI1/SDIO_DATA0), U1.15 (GPIO3/TOUCH3/ADC1_CH2)
/G20: J1.66 (SDIO_DATA1), U1.26 (GPIO45)
/G21: J1.68 (SDIO_DATA2), U1.23 (GPIO21)
/I2C_SCL: J1.14 (I2C_SCL), U1.17 (GPIO9/TOUCH9/ADC1_CH8/FSPIHD/SUBSPIHD)
/I2C_SDA: J1.12 (I2C_SDA), U1.12 (GPIO8/TOUCH8/ADC1_CH7/SUBSPICS1)
/SPI_CIPO-LED_CLK: J1.61 (SPI_SDI), U1.21 (GPIO13/TOUCH13/ADC2_CH2/FSPIQ/FSPIIO7/S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)
/SPI_COPI-LED_DAT: J1.59 (SPI_SDO), U1.19 (GPIO11/TOUCH11/ADC2_CH0/FSPID/FSPIIO5/S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)
/SPI_SCK: J1.57 (SPI_SCK), U1.20 (GPIO12/TOUCH12/ADC2_CH1/FSPICLK/FSPIIO6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)
/UART_RX1: J1.19 (RX1), U1.36 (U0RXD/GPIO44/CLK_OUT2)
/UART_TX1: J1.17 (TX1), U1.37 (U0TXD/GPIO43/CLK_OUT1)
/USB_D+: J1.3 (USB_D+), U1.14 (GPIO20/U1CTS/ADC2_CH9/CLK_OUT1/USB_D+)
/USB_D-: J1.5 (USB_D-), U1.13 (GPIO19/U1RTS/ADC2_CH8/CLK_OUT2/USB_D-)
/~BOOT: J1.11 (~BOOT), R2.2, U1.27 (GPIO0/BOOT)
/~RESET: J1.6 (~RESET), R1.2, U1.3 (EN)
/~SPI_CS: J1.55 (SPI_~CS), U1.18 (GPIO10/TOUCH10/ADC1_CH9/FSPICS0/FSPIIO4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)
GND: C1.2, C2.2, J1.1 (GND), J1.7 (GND), J1.33 (GND), J1.36 (GND), J1.39 (GND), J1.45 (GND), J1.75 (GND), J1.GND1 (GND), J1.GND2 (GND), J1.GND3 (GND), U1.1 (GND), U1.40 (GND), U1.41 (GND)

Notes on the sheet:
Microcontroller
ESP32-S3-WROOM-1
MicroMod Connector
M.2 Connector

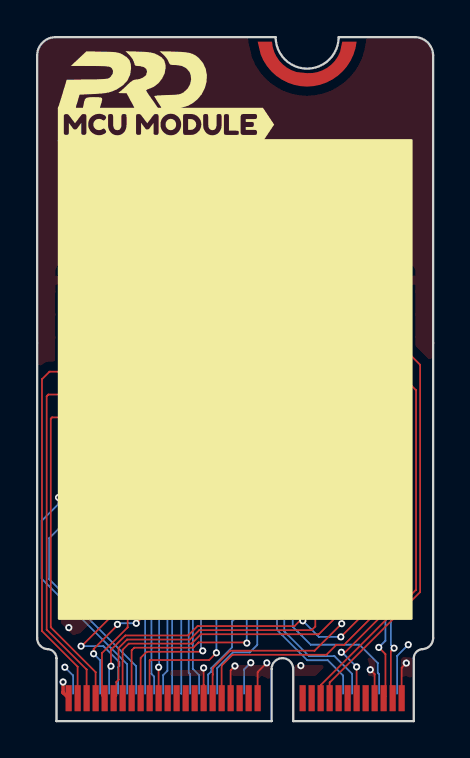
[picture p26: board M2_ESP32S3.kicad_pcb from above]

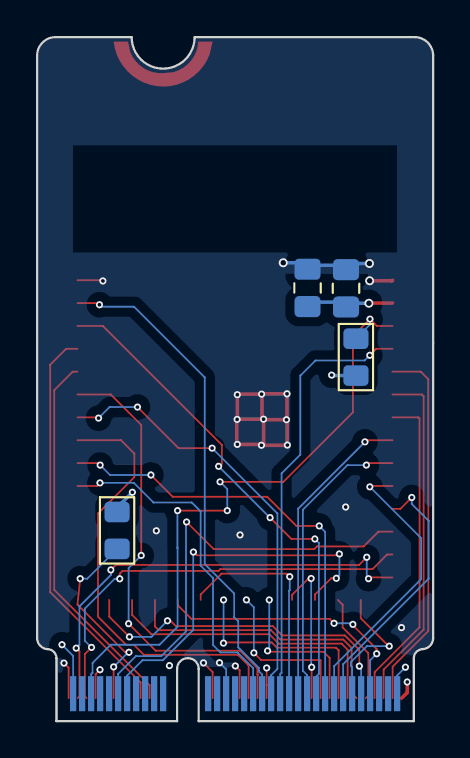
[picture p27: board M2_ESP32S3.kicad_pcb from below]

Board: 4 copper layers, 22.0 x 38.0 mm, 9 parts (4 on the bottom side), 36 nets.

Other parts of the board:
FRAME1: FRAME-LEDGER; CREATIVE_COMMONS
LOGO1: SPECIAL_INSTRUCTIONS-ORDERING; ORDERING_INSTRUCTIONS
kibuzzard-652F57BF: G***; kibuzzard-652F57BF

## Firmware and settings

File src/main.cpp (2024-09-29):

#include <lvgl.h>
#include <Arduino_GFX_Library.h>
#include <driver/twai.h>
#include <driver/gpio.h>
#include <Wire.h>
#include "controllers/uiControl/menu_manager.h"
#include "UI/ui.h"
#include "muTimer.h"
#include "controllers/canBus/can_bus.h"
#include "controllers/uiControl/ui_control.h"
#include "pcb_definitions.h"
#include "controllers/wLed/led_control.h"
#include "soc/gpio_periph.h"
#include "hal/gpio_hal.h"
#include "controllers/uiControl/screen_manager.h"
#include "controllers/rtc/rtc_control.h"
#include "controllers/sensors/bmp280.h"
#include "controllers/uiControl/unit_manager.h"
#include "controllers/comms/comms.h"
#include "controllers/eeprom/eeprom.h"

//  #include "SparkFun_External_EEPROM.h"

#define TFT_BL 2
#define GFX_BL DF_GFX_BL // default backlight pin
#define LGFX_USE_V1
#include <LovyanGFX.hpp>
#include <lgfx/v1/platforms/esp32s3/Panel_RGB.hpp>
#include <lgfx/v1/platforms/esp32s3/Bus_RGB.hpp>

pcb_def pcb;                // pcb definitions struct
rtc_control rtc_controller; // rtc control class
bmp280 bmp280_controller;   // bmp280 control class
Menu_manager menu_manager;

bool pse;
bool entry = true;
int count = 0;

// create a task handler for the leds
TaskHandle_t test_leds_task;

/*******************************************************************************
 * Screen Driver Configuration
 *******************************************************************************/

class LGFX : public lgfx::LGFX_Device
{
public:
  lgfx::Bus_RGB _bus_instance;
  lgfx::Panel_RGB _panel_instance;
  LGFX(void)
  {
    {
      auto cfg = _bus_instance.config();
      cfg.panel = &_panel_instance;
      cfg.pin_d0 = pcb.b0;  // B0
      cfg.pin_d1 = pcb.b1;  // B1
      cfg.pin_d2 = pcb.b2;  // B2
      cfg.pin_d3 = pcb.b3;  // B3
      cfg.pin_d4 = pcb.b4;  // B4
      cfg.pin_d5 = pcb.g0;  // G0
      cfg.pin_d6 = pcb.g1;  // G1
      cfg.pin_d7 = pcb.g2;  // G2
      cfg.pin_d8 = pcb.g3;  // G3
      cfg.pin_d9 = pcb.g4;  // G4
      cfg.pin_d10 = pcb.g5; // G5
      cfg.pin_d11 = pcb.r0; // R0
      cfg.pin_d12 = pcb.r1; // R1
      cfg.pin_d13 = pcb.r2; // R2
      cfg.pin_d14 = pcb.r3; // R3
      cfg.pin_d15 = pcb.r4; // R4
      cfg.pin_henable = pcb.de;
      cfg.pin_vsync = pcb.vsync;
      cfg.pin_hsync = pcb.hsync;
      cfg.pin_pclk = pcb.pclk;
      cfg.freq_write = pcb.prefer_speed;
      cfg.hsync_polarity = pcb.hsync_polarity;
      cfg.hsync_front_porch = pcb.hsync_front_porch;
      cfg.hsync_pulse_width = pcb.hsync_pulse;
      cfg.hsync_back_porch = pcb.hsync_back_porch;
      cfg.vsync_polarity = pcb.vsync_polarity;
      cfg.vsync_front_porch = pcb.vsync_front_porch;
      cfg.vsync_pulse_width = pcb.vsync_pulse;
      cfg.vsync_back_porch = pcb.vsync_back_porch;
      cfg.pclk_active_neg = pcb.pclk_active_neg;
      cfg.de_idle_high = 0;
      cfg.pclk_idle_high = 0;
      _bus_instance.config(cfg);
    }
    {
      auto cfg = _panel_instance.config();
      cfg.memory_width = 800;
      cfg.memory_height = 480;
      cfg.panel_width = 800;
      cfg.panel_height = 480;
      cfg.offset_x = 0;
      cfg.offset_y = 0;
      _panel_instance.config(cfg);
    }
    _panel_instance.setBus(&_bus_instance);
    setPanel(&_panel_instance);
  }
};

LGFX lcd;

/*******************************************************************************
 * Display Driver Configuration
 *******************************************************************************/
#include "touch.h"

static uint32_t screenWidth;
static uint32_t screenHeight;
static lv_disp_draw_buf_t draw_buf;
static lv_color_t disp_draw_buf[DISPLAY_DRAW_BUF];
static lv_disp_drv_t disp_drv;

/* Display flushing */
void my_disp_flush(lv_disp_drv_t *disp, const lv_area_t *area, lv_color_t *color_p)
{
  uint32_t w = (area->x2 - area->x1 + 1);
  uint32_t h = (area->y2 - area->y1 + 1);

#if (LV_COLOR_16_SWAP != 0)
  lcd.pushImageDMA(area->x1, area->y1, w, h, (lgfx::rgb565_t *)&color_p->full);
#else
  lcd.pushImageDMA(area->x1, area->y1, w, h, (lgfx::rgb565_t *)&color_p->full);
#endif

  lv_disp_flush_ready(disp);
}

void my_touchpad_read(lv_indev_drv_t *indev_driver, lv_indev_data_t *data)
{
  if (touch_has_signal())
  {
    if (touch_touched())
    {
      data->state = LV_INDEV_STATE_PR;

      data->point.x = touch_last_x;
      data->point.y = touch_last_y;
      Serial.print("Data x :");
      Serial.println(touch_last_x);

      Serial.print("Data y :");
      Serial.println(touch_last_y);
    }
    else if (touch_released())
    {
      data->state = LV_INDEV_STATE_REL;
    }
  }
  else
  {
    data->state = LV_INDEV_STATE_REL;
  }
}

uint32_t keypad_get_key()
{

  return 0;
}

void keypad_read(lv_indev_drv_t *indev_driver, lv_indev_data_t *data)
{
  static uint32_t last_key = 0;

  /*Get whether the a key is pressed and save the pressed key*/
  uint32_t act_key = menu_manager.getKeyPressed();
  if (act_key != 0)
  {
    data->state = LV_INDEV_STATE_PRESSED;

    /*Translate the keys to LVGL control characters according to your key definitions*/
    switch (act_key)
    {
    case BACK:
      if (lv_obj_has_flag(ui_Menu1, LV_OBJ_FLAG_HIDDEN) == false  && lv_obj_has_flag(ui_Menu2, LV_OBJ_FLAG_HIDDEN) == true){
        lv_obj_add_flag(ui_Menu1, LV_OBJ_FLAG_HIDDEN);
      }else{
        act_key = LV_KEY_PREV;
      }
      break;
    case UP:
      act_key = LV_KEY_LEFT;
      break;
    case DOWN:
      act_key = LV_KEY_RIGHT;
      break;
    case ENTER:
    if (lv_obj_has_flag(ui_Menu1, LV_OBJ_FLAG_HIDDEN) == true){
      lv_obj_clear_flag(ui_Menu1, LV_OBJ_FLAG_HIDDEN);
      lv_group_focus_obj(ui_Menu1);
      lv_roller_set_selected(ui_Menu1, 4, LV_ANIM_OFF);
    }else{
      act_key = LV_KEY_ENTER;
    }
      break;
    case AUX1:
      lv_obj_clear_flag(ui_Menu1, LV_OBJ_FLAG_HIDDEN);
      lv_group_focus_obj(ui_Menu1);
      lv_roller_set_selected(ui_Menu1, 4, LV_ANIM_OFF);
      break;
    }

    last_key = act_key;
    Serial.print("Key: ");
    Serial.println(last_key);
  }
  else
  {
    data->state = LV_INDEV_STATE_RELEASED;
  }

  data->key = last_key;
}

led_control leds; // led control class

/*******************************************************************************
 * Setup Function
 *******************************************************************************/
void setup()
{

  // put your setup code here, to run once:
  Serial.begin(115200); // Init Display

  delay(200);

  lv_init();
  touch_init();

  lcd.begin();
  lcd.fillScreen(TFT_BLACK);
  lcd.setTextSize(2);
  delay(200);

  screenWidth = lcd.width();
  screenHeight = lcd.height();

  lv_disp_draw_buf_init(&draw_buf, disp_draw_buf, NULL, screenWidth * screenHeight / 10);
  //  lv_disp_draw_buf_init(&draw_buf, disp_draw_buf, NULL, 480 * 272 / 10);

  /* Initialize the display */
  lv_disp_drv_init(&disp_drv);

  /* Display resolution */
  disp_drv.hor_res = screenWidth;
  disp_drv.ver_res = screenHeight;
  disp_drv.flush_cb = my_disp_flush;
  disp_drv.draw_buf = &draw_buf;
  lv_disp_drv_register(&disp_drv);

  /* Initialize the (dummy) input device driver */
  if (BOARD_HAS_TOUCH_CAPABILITY)
  {
    static lv_indev_drv_t indev_drv;
    lv_indev_drv_init(&indev_drv);
    indev_drv.type = LV_INDEV_TYPE_POINTER;
    indev_drv.read_cb = my_touchpad_read;
    lv_indev_drv_register(&indev_drv);
  }

  static lv_indev_drv_t indev_drv_buttons;
  lv_indev_drv_init(&indev_drv_buttons);
  indev_drv_buttons.type = LV_INDEV_TYPE_KEYPAD;
  indev_drv_buttons.read_cb = keypad_read;
  lv_indev_t *keypad_indev = lv_indev_drv_register(&indev_drv_buttons);

  if (BOARD_HAS_SLEEP_CAPABILITY)
  {
    gpio_hold_dis(pcb.v5Enable);
    pinMode(pcb.v5Enable, OUTPUT);    // Enable 5V
    digitalWrite(pcb.v5Enable, HIGH); // Enable 5V
    pinMode(pcb.sw12v, INPUT_PULLUP); // 12V Switch
    pinMode(pcb.wakeUp, INPUT_PULLUP); // WakeUp Switch
  }

  initUnitManager(); // Unit Manager Init

  rtc_controller.init_rtc(); // RTC Init

  bmp280_controller.init_bmp280(); // BMP280 Init

  // CAN BUS Init
  canbus_init();

  /* Main UI init Function*/
  ui_init(); // ui from Squareline or GUI Guider

  // UI Initial Configurations
  ui_init_config();

  // Group of UI Elements for control whit menu keys
  lv_group_t *ui_menu_group = lv_group_create();
  lv_group_add_obj(ui_menu_group, ui_Menu1);
  lv_group_add_obj(ui_menu_group, ui_Menu2);
  lv_indev_set_group(keypad_indev, ui_menu_group);
  lv_group_set_default(ui_menu_group);

  // Screen Manager Init
  if (BOARD_HAS_SLEEP_CAPABILITY)
  {
    screen_manager_init();
    _ui_screen_change(&ui_MainScreen, LV_SCR_LOAD_ANIM_OVER_RIGHT, 100, 2000, ui_MainScreen_screen_init);
  }

  if (RMPS_LEDS)
  {
    leds.init_leds();
  }

  if (!BOARD_HAS_SLEEP_CAPABILITY)
  {
    _ui_screen_change(&ui_MainScreen, LV_SCR_LOAD_ANIM_OVER_RIGHT, 100, 2000, ui_MainScreen_screen_init);
  }

  // SerialCommsInit();

#ifdef TFT_BL
  pinMode((gpio_num_t)pcb.tft_bl, OUTPUT);
  analogWrite(pcb.tft_bl, 255);
#endif
}

/*******************************************************************************
 * Main Loop
 *******************************************************************************/
void loop()
{

  lv_timer_handler();

  delay(5);
}

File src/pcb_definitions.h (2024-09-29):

/*!
 * @file pcb_definitions.h
 *
 * This is a file that contains the pcb definitions for the different boards
 * that are supported by the firmware.
 *
 * The pcb_def struct is used to define the pinout of the board and the
 * display parameters.
 *
 * The pcb_def struct is passed to the HardwareInit class to initialize the
 * hardware.
 *
 * Just uncomment the board you are using and comment out the rest.
 *
 * Any custom boards can be added here, just copy and paste the struct and
 * change the pinout and display parameters.
 */

#ifndef PCB_DEFINITIONS_H_
#define PCB_DEFINITIONS_H_

#include <Arduino.h>
#include <Arduino_GFX_Library.h>

/*******************************************************************************
 * Select the board you are using
 *******************************************************************************/

// #define ADVdash7inch
// #define ADVdash7inchV2SD
#define ADVdash5inch

/*******************************************************************************
 * PCB Definitions
 *******************************************************************************/

#if defined(ADVdash5inch)

#define DISPLAY_DRAW_BUF 800 * 480 / 10

#define RMPS_LEDS true
#define INDICATOR_LEDS true
#define LEDS_NUM 18
#define LEDS_PIN 13
#define LEDS_PIN_CLOCK 12
#define LEDS_RPMS_START 4
#define LEDS_RPMS_END 14
#define LEDS_RPMS_LOW 7
#define LEDS_RPMS_MID 10
#define LEDS_RPMS_MAX 14

// Can Bus Transceiver Pins
// #define CAN_TX_PIN GPIO_NUM_13
// #define CAN_RX_PIN GPIO_NUM_12

#define CAN_TX_PIN GPIO_NUM_44
#define CAN_RX_PIN GPIO_NUM_43

#define BOARD_HAS_SLEEP_CAPABILITY true
#define BOARD_HAS_TOUCH_CAPABILITY true
#define ENABLE_ALERTS false

struct pcb_def
{

    // ESP32RGBPANEL
    int8_t tft_bl = 2;
    int8_t cs = GFX_NOT_DEFINED;
    int8_t sck = GFX_NOT_DEFINED;
    int8_t sda_display = GFX_NOT_DEFINED;
    int8_t de = GPIO_NUM_40;
    int8_t vsync = GPIO_NUM_41;
    int8_t hsync = GPIO_NUM_39;
    int8_t pclk = GPIO_NUM_0;
    int8_t r0 = GPIO_NUM_45;
    int8_t r1 = GPIO_NUM_48;
    int8_t r2 = GPIO_NUM_47;
    int8_t r3 = GPIO_NUM_21;
    int8_t r4 = GPIO_NUM_14;
    int8_t g0 = GPIO_NUM_5;
    int8_t g1 = GPIO_NUM_6;
    int8_t g2 = GPIO_NUM_7;
    int8_t g3 = GPIO_NUM_15;
    int8_t g4 = GPIO_NUM_16;
    int8_t g5 = GPIO_NUM_4;
    int8_t b0 = GPIO_NUM_8;
    int8_t b1 = GPIO_NUM_3;
    int8_t b2 = GPIO_NUM_46;
    int8_t b3 = GPIO_NUM_9;
    int8_t b4 = GPIO_NUM_1;
    uint16_t width = 800;
    uint16_t hsync_polarity = 0;
    uint16_t hsync_front_porch = 8;
    uint16_t hsync_pulse = 4;
    uint16_t hsync_back_porch = 43;
    uint16_t height = 480;
    uint16_t vsync_polarity = 0;
    uint16_t vsync_front_porch = 8;
    uint16_t vsync_pulse = 4;
    uint16_t vsync_back_porch = 12;
    uint16_t pclk_active_neg = 1;
    int32_t prefer_speed = 15000000;
    bool auto_flush = true;

    // GPIO
    gpio_num_t v5Enable = GPIO_NUM_17;
    gpio_num_t sw12v = GPIO_NUM_10;
    gpio_num_t wakeUp = GPIO_NUM_11;

    int sda_touch = 38;
    int scl_touch = 42;
};

enum ledPosition
{
    HIGH_BEAM,
    BATTERY_LIGHT,
    CHECK_ENGINE,
    LEFT_DIR,
    RIGHT_DIR = 14,
    OIL_PRESSURE_LED,
    PARKING_BRAKE,
    FUEL_LED
};

#endif

#if defined(ADVdash7inch)

#define DISPLAY_DRAW_BUF 800 * 480 / 10

#define RMPS_LEDS false
#define INDICATOR_LEDS false
#define LEDS_NUM 18
#define LEDS_PIN 38
#define LEDS_RPMS_START 4
#define LEDS_RPMS_END 14
#define LEDS_RPMS_LOW 7
#define LEDS_RPMS_MID 10
#define LEDS_RPMS_MAX 14

// Can Bus Transceiver Pins
#define CAN_TX_PIN GPIO_NUM_18
#define CAN_RX_PIN GPIO_NUM_17

#define BOARD_HAS_SLEEP_CAPABILITY false
#define BOARD_HAS_TOUCH_CAPABILITY true

struct pcb_def
{

    // ESP32RGBPANEL
    int8_t tft_bl = 2;
    int8_t cs = GFX_NOT_DEFINED;
    int8_t sck = GFX_NOT_DEFINED;
    int8_t sda_display = GFX_NOT_DEFINED;
    int8_t de = 41;
    int8_t vsync = 40;
    int8_t hsync = 39;
    int8_t pclk = 42;
    int8_t r0 = 14;
    int8_t r1 = 21;
    int8_t r2 = 47;
    int8_t r3 = 48;
    int8_t r4 = 45;
    int8_t g0 = 9;
    int8_t g1 = 46;
    int8_t g2 = 3;
    int8_t g3 = 8;
    int8_t g4 = 16;
    int8_t g5 = 1;
    int8_t b0 = 15;
    int8_t b1 = 7;
    int8_t b2 = 6;
    int8_t b3 = 5;
    int8_t b4 = 4;
    uint16_t width = 800;
    uint16_t hsync_polarity = 0;
    uint16_t hsync_front_porch = 210;
    uint16_t hsync_pulse = 30;
    uint16_t hsync_back_porch = 16;
    uint16_t height = 480;
    uint16_t vsync_polarity = 0;
    uint16_t vsync_front_porch = 22;
    uint16_t vsync_pulse = 13;
    uint16_t vsync_back_porch = 10;
    uint16_t pclk_active_neg = 1;
    int32_t prefer_speed = 12000000;
    bool auto_flush = true;

    // GPIO
    gpio_num_t v5Enable = GPIO_NUM_NC;
    gpio_num_t sw12v = GPIO_NUM_NC;
    gpio_num_t wakeUp = GPIO_NUM_NC;
};

enum ledPosition
{
    HIGH_BEAM,
    BATTERY_LIGHT,
    CHECK_ENGINE,
    LEFT_DIR,
    RIGHT_DIR = 14,
    OIL_PRESSURE_LED,
    PARKING_BRAKE,
    FUEL_LED
};

#endif

#if defined(ADVdash7inchV2SD)
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

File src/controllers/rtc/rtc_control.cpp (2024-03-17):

#include <Arduino.h>
#include <SparkFun_RV8803.h>
#include "rtc_control.h"

RV8803 rtc;

void rtc_control::init_rtc()
{

    if (rtc.begin() == false)
    {
        Serial.println("RTC failed to initialize!");
    }
    else
    {
        Serial.println("RTC initialized successfully.");
    }
    /*
    if (rtc.setToCompilerTime() == false)
        Serial.println("Something went wrong setting the time");
    else
        Serial.println("New time set!");
        */
        
}

rtc_date rtc_control::get_date()
{

    rtc_date date;

    if (rtc.updateTime())
    {
        date.day = rtc.getDate() < 10 ? "0" + String(rtc.getDate()) : String(rtc.getDate());
        date.month = rtc.getMonth() < 10 ? "0" + String(rtc.getMonth()) : String(rtc.getMonth());
        date.year = rtc.getYear() < 10 ? "0" + String(rtc.getYear()) : String(rtc.getYear());
    }

    return date;
}

rtc_time rtc_control::get_time()
{

    rtc_time time;

    if (rtc.updateTime())

    {
        // agregar un 0 a la izquierda si el valor es menor a 10
        time.seconds = rtc.getSeconds() < 10 ? "0" + String(rtc.getSeconds()) : String(rtc.getSeconds());
        time.minutes = rtc.getMinutes() < 10 ? "0" + String(rtc.getMinutes()) : String(rtc.getMinutes());
        time.hours = rtc.getHours() < 10 ? "0" + String(rtc.getHours()) : String(rtc.getHours());
    }

    return time;
}

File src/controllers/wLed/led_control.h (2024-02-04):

#ifndef LED_CONTROL_H
#define LED_CONTROL_H

#include "pcb_definitions.h"

enum ledState
{
    LED_OFF,
    LED_ON,
    LED_BLINK
};

enum ledColor
{
    LED_RED = 0xff0000,
    LED_GREEN = 0x00ff00,
    LED_BLUE = 0x0000ff,
    LED_YELLOW = 0xffff00,
    LED_PURPLE = 0xff00ff,
    LED_CYAN = 0x00ffff,
    LED_WHITE = 0xffffff
};

struct indicatorLedState
{
    bool HighBeamST = false;
    bool LeftTurnST = false;
    bool RightTurnST = false;
    bool ParkingST = false;
    bool BatteryST = false;
    bool OilPressureST = false;
    bool CheckEngineST = false;
    bool FuelST = false;

};

struct indicatorLedStatePrevious
{
    bool HighBeamST = true;
    bool LeftTurnST = true;
    bool RightTurnST = true;
    bool ParkingST = true;
    bool BatteryST = true;
    bool OilPressureST = true;
    bool CheckEngineST = true;
    bool FuelST = true;

};

void ledControlTask(void *pvParameters);
void commitTaskProcedure(void *arg);
void commit();

class led_control
{

public:
    void init_leds();
    static void ledsWelcomeAnimation(void *pvParameters);
    void triggerWelcomeAnimation();
    void clearLeds();
    
    // void setIndicatorLeds(ledState state, ledPosition position ,ledColor color);
};

#endif // LED_CONTROL_H

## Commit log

2023-09-27 can bus, database, ui control classes implementations
    [BenchTest.stl]
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2023-09-29 xQueue for send data from Can Bus to ui control
2023-10-04 RPMS bar issue #2 corrected, panels and tps bar classes ok
    [gp_panel.cpp, ui_control.cpp]
2023-10-12 Save Settings BTN working, long press for reset and restore defaults
    [ui_control.cpp]
2023-10-19 Hardware directory added
    [AdvDash_5_inch.kicad_pcb, AdvDash_5_inch.kicad_sch, ESP32S3_M2_Pinout.xlsx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]
2023-10-27 R0.1.0 PCB added
    [AdvDash_5_inch.kicad_pcb, AdvDash_5_inch.kicad_sch, ConnectorPCB.kicad_pcb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]
2023-11-01 PCB R0.1.0
    [AdvDash_5_inch.kicad_pcb, AdvDash_5_inch.kicad_sch, ConnectorPCB.kicad_pcb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]
2023-12-26 :white_check_mark: Add STL files and some renders off the of the casing
    [CaseSup.stl, Caseinf.stl]
2023-12-26 :adhesive_bandage: Minor change to the PCB
    [AdvDash_5_inch.csv, AdvDash_5_inch.kicad_pcb, ConnectorPCB.kicad_pcb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]
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2023-12-28 :adhesive_bandage: Fix errors in pcb desing, changelog in file, rev0.2.0
    [AdvDash_5_inch.kicad_sch, bmp280.kicad_sch, canbus.kicad_sch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]
2023-12-28 :white_check_mark: Dxf files for acrilic parts, new case top part
    [AcrilicoINF.dxf, AcrilicoSUP.dxf, AcrilicoSUP2.dxf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]
2023-12-28 :art: Introduce pcb definition file, clean up in main.c
2023-12-30 :sparkles: RGB leds control added, leds welcome animation logic complete
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2023-12-31 :art: Improve pcb definitions to work whit 7 inch board
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2024-01-02 :loud_sound: Now if there is any error in the can driver it prints it in the Serial Console
    [can_bus.cpp]
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2024-01-03 :alembic: Firts test of control logic for indicators leds
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2024-01-03 :art: [ADD] Definitions related to indicator leds, new enums for indicador leds control
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2024-01-07 :bug: PCB R0.2.0 Ready, change log in kicad files
    [AdvDash_5_inch.kicad_pcb, AdvDash_5_inch.kicad_sch, connector.kicad_sch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]
2024-01-07 :arrow_up: Change Fastled library to test more stable library on esp32
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2024-02-04 :bug: [FIX] Solution to several errors in the pcb design, log of changes in kicad files
    [AdvDash_5_inch.kicad_pcb, bom.csv, designators.csv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]
2024-02-04 :bug: [FIX] Added space to access the display connector without desoldering the main connector
    [ConnectorPCB.kicad_pcb, bom.csv, designators.csv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]
2024-02-04 :lipstick: [UI] New welcome screen, changes to the main screen, it now has 3 buttons, new panel with time and temperature information
2024-02-04 :zap: [CANBUS] Change in data sent to queue, fuel data is removed
2024-02-04 :zap: [FIX] LED replacement for SK9822 due to poor performance with only 1 data line
    [led_control.h]
2024-02-04 :sparkles: [ADD] New pcb options for LEDs and Sleep functions
2024-02-04 :bug: [FIX] New i2c pins for new board
2024-02-04 :sparkles: [ADD] Atmosferic atmospheric pressure and temperature data added (BMP180)
2024-02-04 :bookmark: [PCB] Main PCB R0.2.0
    [bom.csv, designators.csv, positions.csv]
2024-02-04 :bug: [FIX] Change some convertions values
    [can_bus.cpp]
2024-02-04 :zap: [FIX] Delete condition on main canbus loop
    [ui_control.cpp]
2024-02-04 :sparkles: [ADD] Canbus data factor correction to show correct values
    [gp_panel.cpp]
2024-02-04 :bug: [FIX] New defaults and alerts for corrected canbus values
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2024-03-17 :poop: Development is resumed after a long time, I have no idea what was modified before, let's hope for the best, last change, now in the time and date a 0 was added at the beginning if the number i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
    [AdvDash_5_inch-B_Silkscreen.dxf, AdvDash_5_inch-F_Silkscreen.dxf, AdvDash_5_inch.kicad_pcb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]
2024-04-05 :bug: [FIX] Change TPS encode value
    [can_bus.cpp]
2024-04-05 :bug: [FIX] TPS value in canbus_data_t was uint_8, change for uint_16
2024-04-05 :bug: [FIX] Battery Bar Colors fix, tps bar FIX
2024-04-05 :zap: [FIX] Now the backlight only turn on at the end of setup
    [main.cpp]
2024-04-05 :art: New GitIgnore
    [PCU-8D.STEP]
2024-04-06 :art: [FIX] Changes to implement the new database structure
    [alert_manager.h]
2024-04-07 :poop: Testing new values for led control, not working
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2024-04-14 🎨 Refactor database.cpp to add vscode minimap new sections
2024-04-15 ✨ Refactor alert_manager.cpp and alert_manager.h to improve alert handling, not tested
2024-04-16 🐛 Refactor can_bus.cpp to handle temperature values within a specific range
2024-04-16 🐛 Refactor alert_manager.cpp to fix alert calculations and display values in criticalPanel
2024-04-16 ♻️ change default value for FUEL_PRESSURE_LOW_ALERT in database.h
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2024-04-22 ✏️ Fix typo in database.cpp comments
2024-04-23 🩹 turn off serial debug for can bus comms
2024-04-23 💩 TS test port causes reset
    [comms.cpp]
2024-04-23 🚧 Add SerialCommsInit() function call in setup() to initialize serial communication
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2024-04-28 🎨 Update PCB pin assignments and configuration in main.cpp and pcb_definitions.h
2024-04-28 ✨ Update PCB pin assignments and configuration for ADVdash7inchV2SD in pcb_definitions.h
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2024-04-28 💩 Fix typo in codeVersion array initialization
    [comms.cpp]
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2024-04-28 ✏️ Fix typo in ADVdashDev.ini
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2024-04-29 🐛 Update TOUCH_MAP_X2 for correct touch calibration
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2024-04-29 ✨ Refactor gp_arc class to change user setting on the go
2024-04-29 🚧 Now the user settings happen in the main screen
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2024-04-30 💄 Now, config panel show in the correct place
2024-04-30 ✨ Add gearPanel and speedPanel classes for UI control widgets
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2024-06-15 🎨 Refactor code to improve readability and remove unnecessary comments
2024-06-15 🚀 PCB R0.2.1
    [AdvDash_5_inch.csv, AdvDash_5_inch.kicad_pcb, AdvDash_5_inch.kicad_sch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]
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2024-06-15 💄 Refactor UI code to add oil press image and container
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2024-06-16 ✨ New CanBus Messages Added, Debug Prints with macros
2024-06-16 🐛 Added Macro pdMS_TO_TICKS for the queue wait time
2024-06-16 🐛 Fix led logic remove data from the queue before uicontrol, change to xQueuePeek
2024-06-22 ⚡️ Time to wait for CanBus Frame changed to 0
2024-06-22 ✨ Add menu button messages to Can Database
2024-06-30 ✨ Update rus_efi_can_verbose.c with new pack and unpack functions
2024-06-30 💄 New Left menu and trip info section
2024-06-30 ✨ Add new CAN messages and update CAN data struct
2024-06-30 ✨ Add menu button logic and menu manager file
2024-06-30 💄 New menu for user, new trip info window
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2024-09-22 New CAD desing for Bike
    [DifusorGrande.stl, DifusorPequeno.stl, InferiorMoto.stl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]
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2024-09-22 ✨ Refactor UI control code and add EEPROM manager
2024-09-22 ♻️ Refactor UI control code and add EEPROM manager
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2024-09-25 ⚡️ Refactor canbus_read function to update current_gear value from rus_efi_can_verbose_base0 instead of rus_efi_can_verbose_pro0
2024-09-25 ✨ New Frame for Gateway data from dashController
2024-09-25 Add 12V and WakeUp switch pin modes in setup()
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2024-09-27 ⚡️ Refactor LED control code to use FastLED library
2024-09-27 Refactor LED control code to disable FastLED interrupts
2024-09-27 ♻️ Refactor QS Lua and LED control code
    - In TT250Lua.txt, invert the value of qsTimingAdd setting
    - In TT250Lua.txt, divide qsDuration by 1000
    - In led_control.cpp, change the priority of ledControlTask and ShowRunnerTask to 2
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2024-09-28 ✨ Introduce Dash Icons widget and refactor LED control code
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2024-09-28 ⚡️ Refactor data rate cycle triggers in ui_control.cpp
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2024-09-29 🐛 Error Fix, Crash at boot
2024-09-29 ⚡️ New timer for icons data rate, Revert change in main data rate
    [ui_control.cpp]
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2024-09-29 ✨ Add fuel trim, fuel flow, and fuel used data to canbus_read function
2024-09-29 ✨ Add support for new gauge types in UI control
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2024-09-30 Fix tire pressure display precision in gp_panel widget
    [gp_panel.cpp]
2024-09-30 Fix tire pressure display precision in canbus_encode struct
    [can_bus.cpp]
2024-09-30 🐛 Fix out-of-range value in tpsBar::setValue function
2024-09-30 🐛 Fix tire pressure display precision in canbus_encode struct
    [can_bus.cpp]
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2025-08-10 Refactor gp_panel.cpp and update KiCad project settings
    Removed unnecessary whitespace and improved formatting in gp_panel.cpp. Updated fuel used calculation logic. Added new DRC and BOM settings to AdvDash_5_inch.kicad_pro. Updated .gitignore to exclude 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

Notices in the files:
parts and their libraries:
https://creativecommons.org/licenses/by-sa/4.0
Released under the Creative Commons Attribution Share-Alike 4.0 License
